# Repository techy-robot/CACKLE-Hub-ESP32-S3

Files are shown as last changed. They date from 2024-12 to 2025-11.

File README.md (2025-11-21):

---
modified: 2025-11-07T22:07:35-07:00
---

# ESP32-S3 Hub

> [!TIP]
> This board is part of a larger modular control board ecosystem, [CACKLE](https://github.com/techy-robot/CACKLE)

This is a 4-driver hub based on the Espressif ESP32-S3FH4 chip. It has two cores powerful running at 240 mhz, and 4mb of flash memory. Other variants of the ESP32-S3 can be used as long as they have built in flash memory.

The ESP32-S3 chip does not *quite* have enough pins for driving 4 motors and several sensors, so some cuts were made. For example, on all 4 ports for the ADCs, only two out of three pins are actually connected. This will work for brushed and brushless FOC control, but it may not work for other use cases. I also had to use the USB lines for a tri-state shift register, which controls all the SPI chip select lines. I am planning on programming the chip via UART, which means that the RS485 lines must be disconnected.

The SPI bus should be able to operate at 80mhz, though this has not been tested yet. For all practical use-cases I am limiting this to 20mhz.

Schematic PDF

Partial 3D picture (headers not shown)
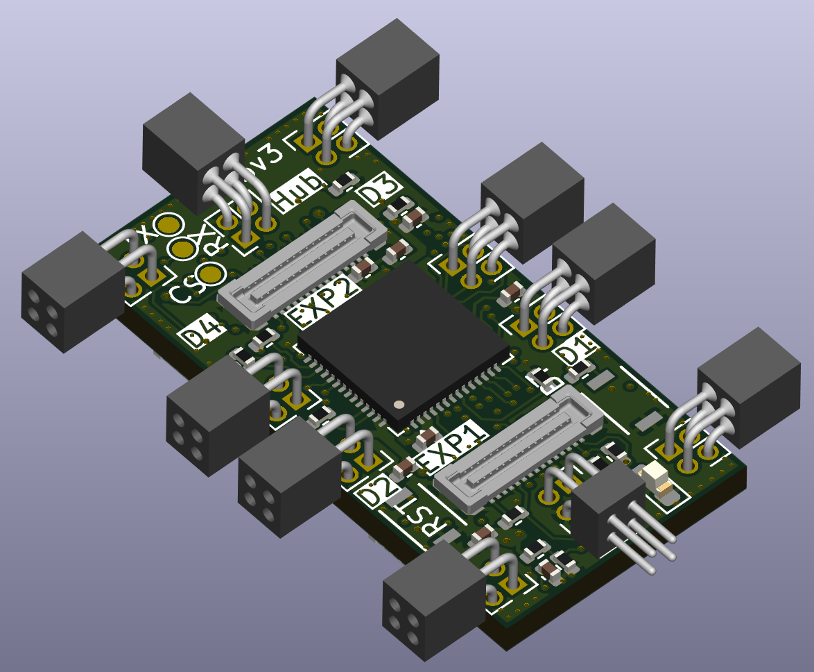
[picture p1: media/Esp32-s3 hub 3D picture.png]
Esp32-s3 hub 3D picture


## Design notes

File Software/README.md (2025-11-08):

# Software

This is based on [Luos Engine](https://www.luos.io/), a lightweight distributed communication engine that aims to make hardware as modular as software. 

Most of the code found here are luos node definitions and driver services for the of the hardware modules, designed to be easily reusable in your project. There are also some tests and example code.

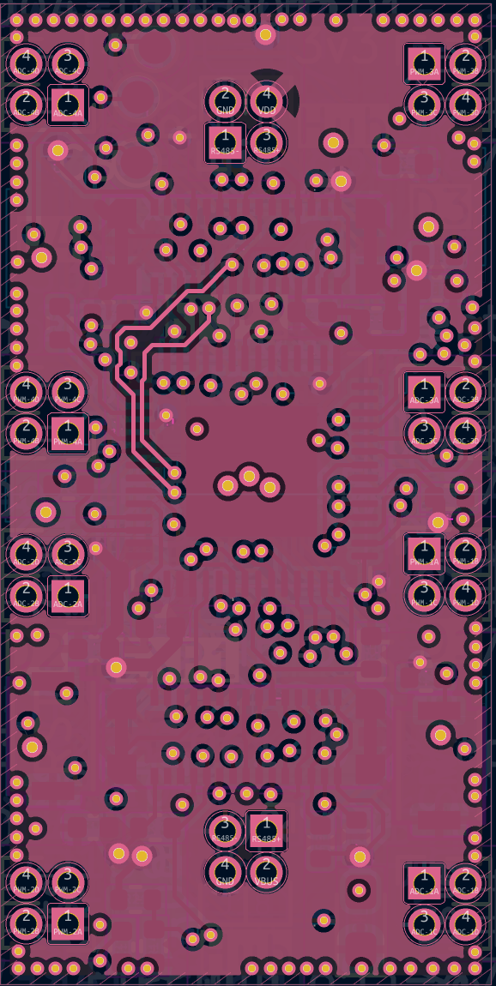
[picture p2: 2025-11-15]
media/ESP32-S3 hub In4.png

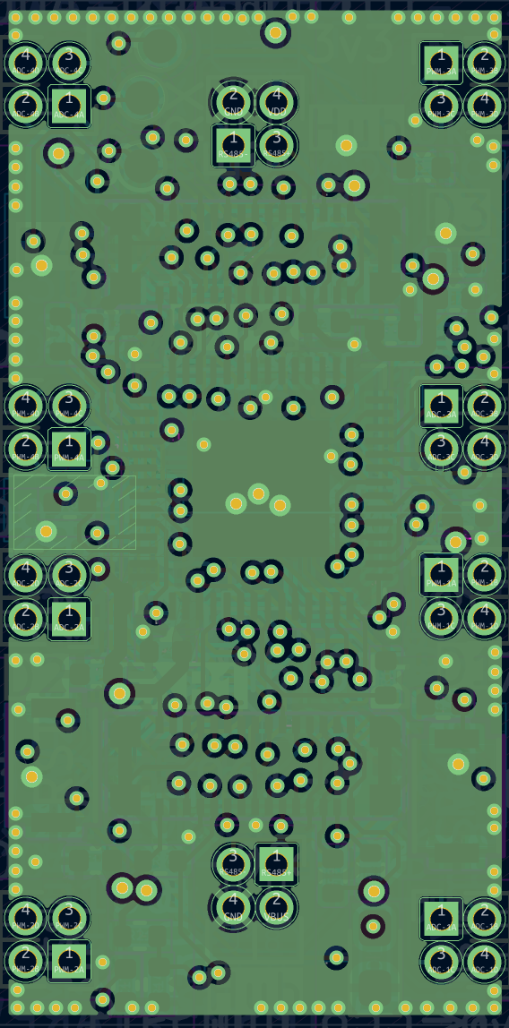
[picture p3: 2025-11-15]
media/ESP32-S3 hub In1.png

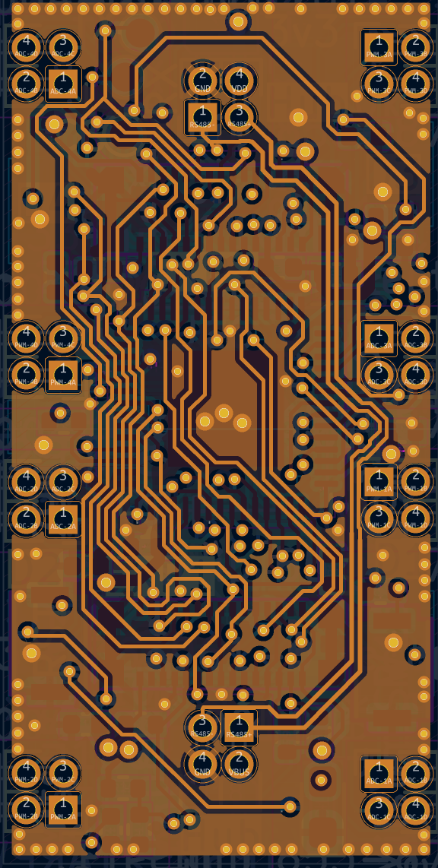
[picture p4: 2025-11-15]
media/ESP32-S3 hub In2.png

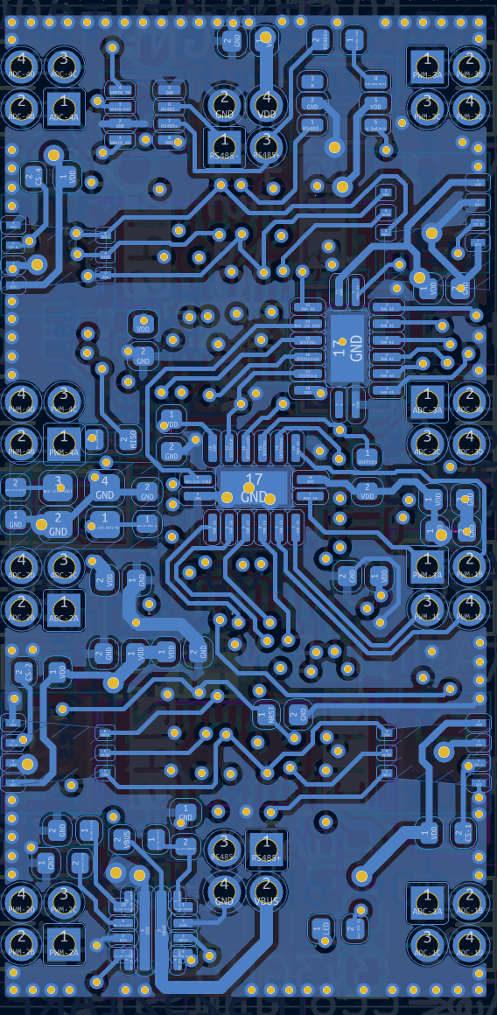
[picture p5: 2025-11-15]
media/ESP32-S3 hub Bottom.png

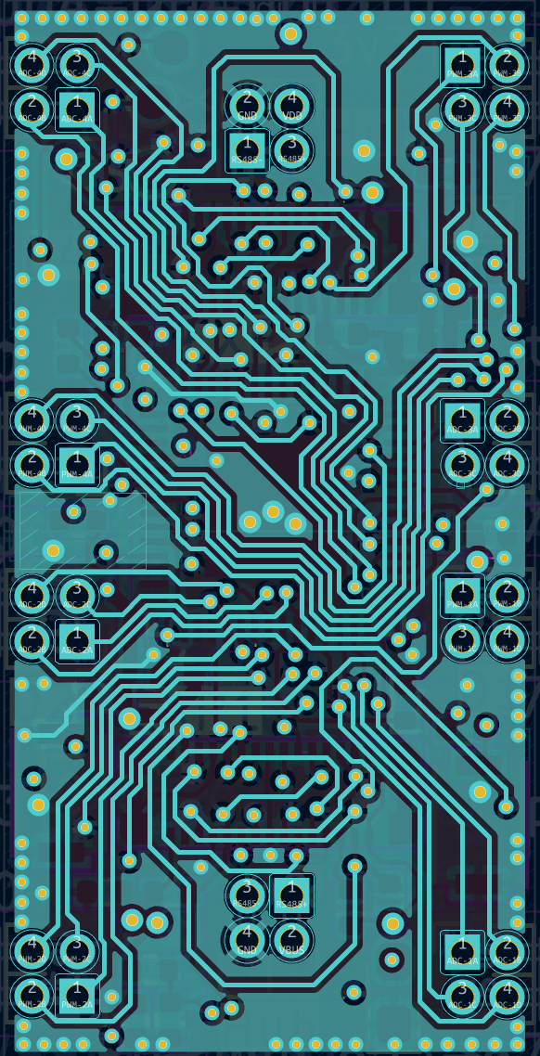
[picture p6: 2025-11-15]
media/ESP32-S3 hub In3.png

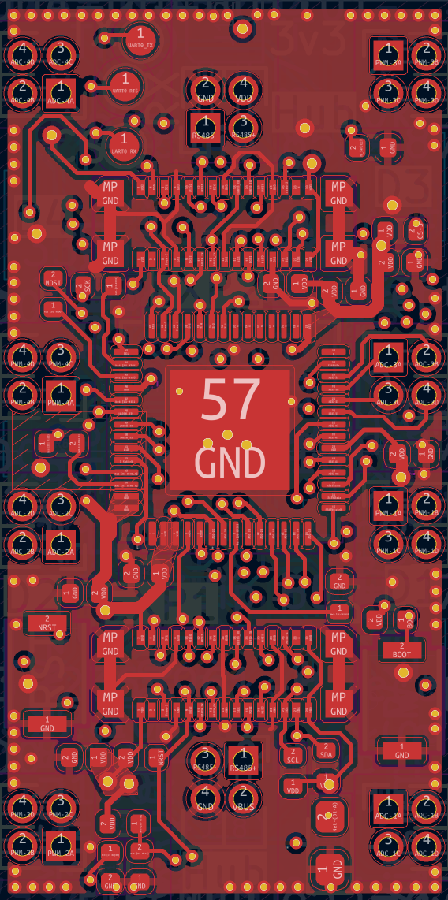
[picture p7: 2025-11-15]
media/ESP32-S3 hub Top.png

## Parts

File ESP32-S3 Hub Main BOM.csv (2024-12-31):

Id | Designator | Footprint | Quantity | Designation | Supplier and ref
1 | D1 | LED_0603_1608Metric_Pad1.05x0.95mm_HandSolder | 1 | 2.6~3.1 Fv Green 5ma
2 | J22 | PinHeader_1x04_P1.27mm_Horizontal | 1 | 1.27mm 4 pin header
3 | C13,C9,C2,C7 | C_0402_1005Metric | 4 | 1uF
4 | C10,C4,C6,C8,C5,C3 | C_0402_1005Metric | 6 | 0.1uF
5 | R8,R9,R7,R20,R19,R11,R18,R2 | R_0402_1005Metric | 8 | 10k
6 | J10,J6,J2,J1,J7,J12,J4,J9 | PinHeader_1x03_P1.27mm_Vertical | 8 | 1.27mm 3pin socket
7 | C12,C11 | C_0402_1005Metric | 2 | 12pF
8 | SW2,SW1 | R-667995_MIT | 2 | Mitsumi R-667996
9 | Y1 | Crystal_SMD_2016-4Pin_2.0x1.6mm | 1 | ABM11-40.000MHZ-B1U-T3, 10ppm, 10pF
10 | FB1 | L_0402_1005Metric | 1 | 120ohm imp @100mhz, 1 amp
11 | U1 | QFN-56-1EP_7x7mm_P0.4mm_EP4x4mm | 1 | ESP32-S3
12 | J16,J13 | TE_mezzanine_rec_3-2363961-0 | 2 | TE 3-2363961-0 receptacle
13 | J21 | PinSocket_1x04_P1.27mm_Vertical | 1 | 1.27mm 4 pin socket
14 | R6 | R_0402_1005Metric | 1 | 22 ohm
15 | R1 | R_0402_1005Metric | 1 | 100k
16 | R10 | R_0402_1005Metric | 1 | 80.6 ohm
17 | C1,C14 | C_0402_1005Metric | 2 | 22uF
18 | U2 | DHVQFN-16-1EP_2.5x3.5mm_P0.5mm_EP1x2mm | 1 | 74HC595
19 | R3,R4,R5 | R_0402_1005Metric | 3 | 33ohm
20 | J14,J17 | TE_mezzanine_conn_3-2363962-0 | 2 | TE 3-2363962-0 Connector
21 | J11,J8,J5,J3 | fpc_7pin_0.3mm_connector Panasonic | 4 | 7 pin FPC 0.3mm Panasonic Y3b
22 | U3 | SOT-583-8 | 1 | THVD1420DRLR

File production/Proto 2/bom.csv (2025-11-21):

Designator | Footprint | Quantity | Value | LCSC Part #
C1, C14 | 402 | 2 | 22uF | C415703
C10, C4, C5, C6, C8 | 402 | 5 | 100nF | C1525
C11, C12 | 201 | 2 | 12pF | C384960
C13, C15, C16, C2, C7, C9 | 402 | 6 | 1uF | C52923
C17 | 402 | 1 | 3.3nF | C272874
C18 | 402 | 1 | 2.7nF | C541392
C19, C20, C21, C22 | 402 | 4 | 10nF | C318576
C3 | 402 | 1 | 10uF | C15525
D1 | 603 | 1 | 2.6~3.1 Fv Green 5ma | C3028858
J1, J10, J12, J15, J2, J4, J6, J7, J9 | Precidip 853-87-004-20-001101 | 9 | Precidip 853-87-004-20-001101
J11, J3, J5, J8 | fpc_7pin_0.3mm_connector Aces | 4 | FPC 0.3mm Aces 51688-0070M
J13, J16 | TE_mezzanine_rec_3-2363961-0 | 2 | TE 3-2363961-0 receptacle | C425103
J18 | Precidip 852-10-004-20-001101 | 1 | Precidip 852-10-004-20-001101
R1, R14 | 402 | 2 | 100k | C25741
R10 | 402 | 1 | 100 ohm | C185392
R11 | 402 | 1 | 470k | C25790
R12 | 402 | 1 | 332k | C138005
R13, R17, R18, R19, R2, R20, R22, R7 | 402 | 8 | 10k | C25744
R15 | 402 | 1 | 6.04k | C321224
R16 | 402 | 1 | 120ohm | C25079
R21 | 402 | 1 | 150k | C25755
R3, R4, R5 | 402 | 3 | 33ohm | C25105
R6 | 201 | 1 | 22 ohm | C155743
R8, R9 | 402 | 2 | 2.2k | C25879
SW1, SW2 | R-667995_MIT | 2 | Mitsumi R-667996 | C4365007
U1 | QFN-56-1EP_7x7mm_P0.4mm_EP4x4mm | 1 | ESP32-S3 FN8 | C3013940
U2, U5 | DHVQFN-16-1EP_2.5x3.5mm_P0.5mm_EP1x2mm | 2 | SN74LV595A | C7083313
U3 | SOT-583-8 | 1 | THVD1420DRLR | C3235555
U4 | QFN-10_10VQFN_2x2mm_P0.5mm | 1 | TPS2521ARPWR | C3662707
U6 | SOT-363_SC-70-6 | 1 | TS5A3159DCK | C46388
Y1 | Crystal_SMD_1612-4Pin_1.6x1.2mm | 1 | 2 pin 40MHZ, 10ppm tol., 20ppm stab., 10pF | C49158191

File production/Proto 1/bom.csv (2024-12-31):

Designator | Footprint | Quantity | Value | LCSC Part #
C1, C14 | 0402 | 2 | 22uF | C415703
C10, C3, C4, C5, C6, C8 | 0402 | 6 | 0.1uF | C1525
C11, C12 | 0402 | 2 | 12pF | C1547
C13, C2, C7, C9 | 0402 | 4 | 1uF | C52923
D1 | 0603 | 1 | 2.6~3.1 Fv Green 5ma | C3028858
FB1 | 0402 | 1 | 120ohm imp @100mhz, 1 amp | C82861
J13, J16 | TE_mezzanine_rec_3-2363961-0 | 2 | TE 3-2363961-0 receptacle | C425103
J14, J17 | TE_mezzanine_conn_3-2363962-0 | 2 | TE 3-2363962-0 Connector | C425104
R1 | 0402 | 1 | 100k | C25741
R10 | 0402 | 1 | 80.6 ohm | C185392
R11, R18, R19, R2, R20, R7, R8, R9 | 0402 | 8 | 10k | C25744
R3, R4, R5 | 0402 | 3 | 33ohm | C25105
R6 | 0402 | 1 | 22 ohm | C25092
SW1, SW2 | R-667995_MIT | 2 | Mitsumi R-667996 | C4365007
U1 | QFN-56-1EP_7x7mm_P0.4mm_EP4x4mm | 1 | ESP32-S3 | C3013940
U2 | DHVQFN-16-1EP_2.5x3.5mm_P0.5mm_EP1x2mm | 1 | 74HC595 | C730243
Y1 | Crystal_SMD_2016-4Pin_2.0x1.6mm | 1 | ABM11-40.000MHZ-B1U-T3, 10ppm, 10pF | C648973

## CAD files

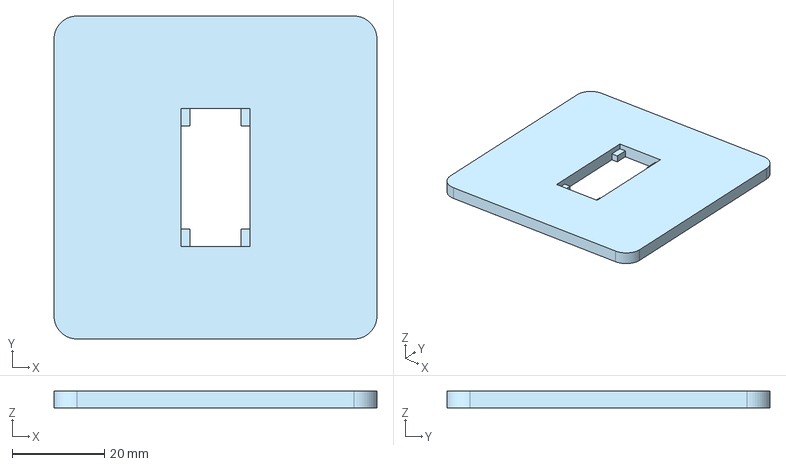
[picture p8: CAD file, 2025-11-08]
ESP32-S3 2nd side Stencil Jig.step
70.0 x 70.0 x 3.60 mm

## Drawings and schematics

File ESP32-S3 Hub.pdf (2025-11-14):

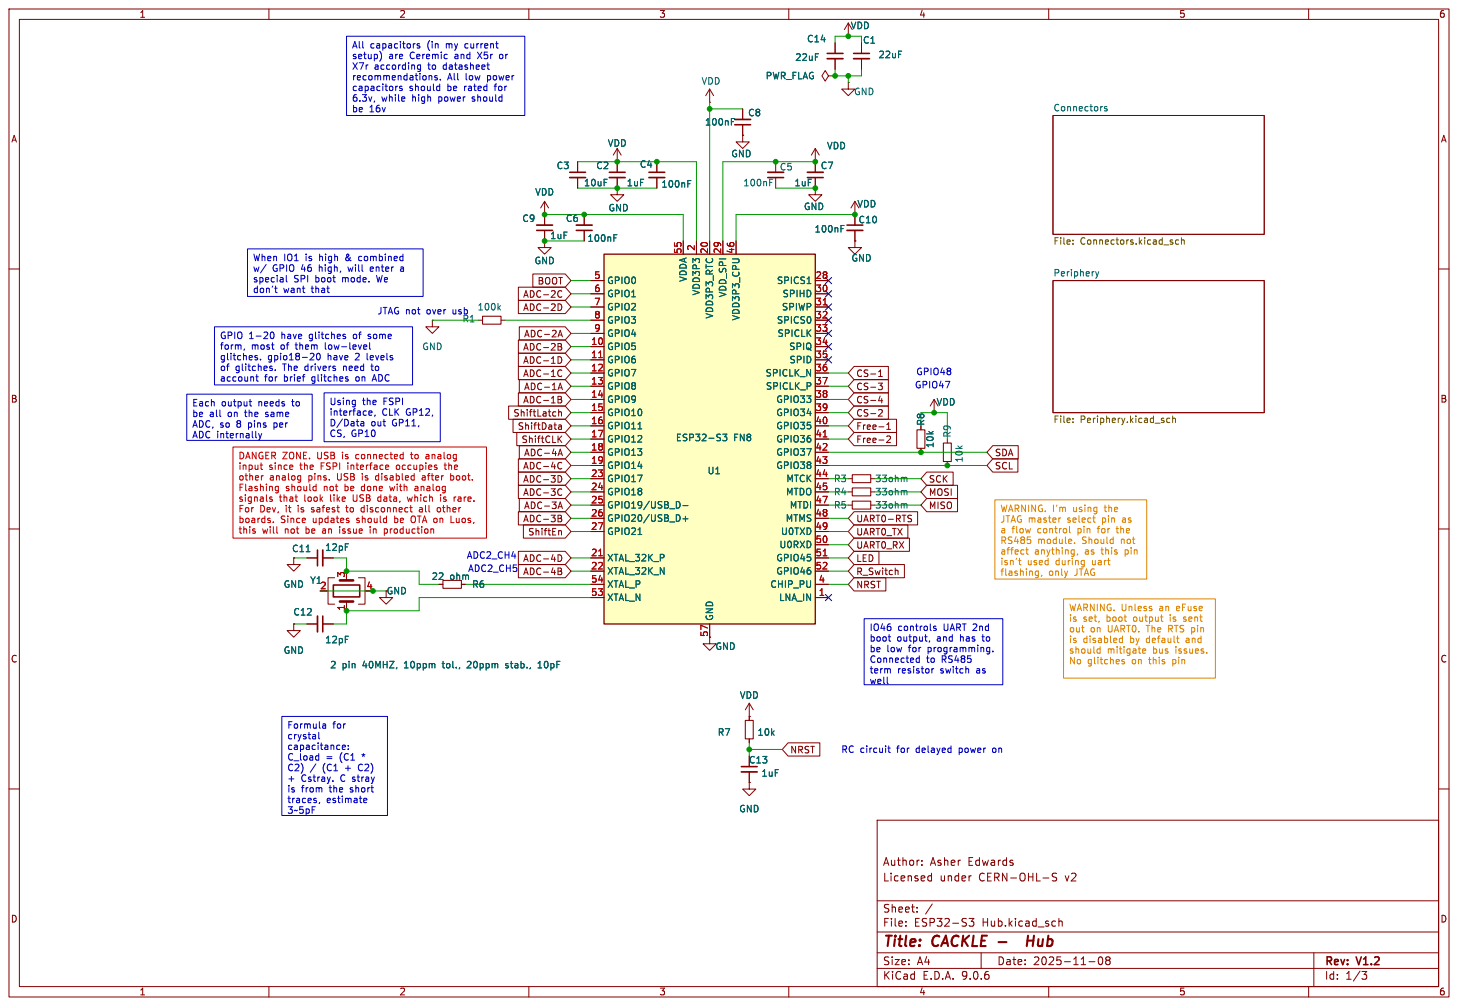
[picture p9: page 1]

Periphery File: Periphery.kicad_sch Connectors File: Connectors.kicad_sch C6

special SPI boot mode. We

this will not be an issue in production

isn't used during uart

boot output, and has to
be low for programming. Connected to RS485

is set, boot output is sent out on UART0. The RTS pin

is from the short
traces, estimate

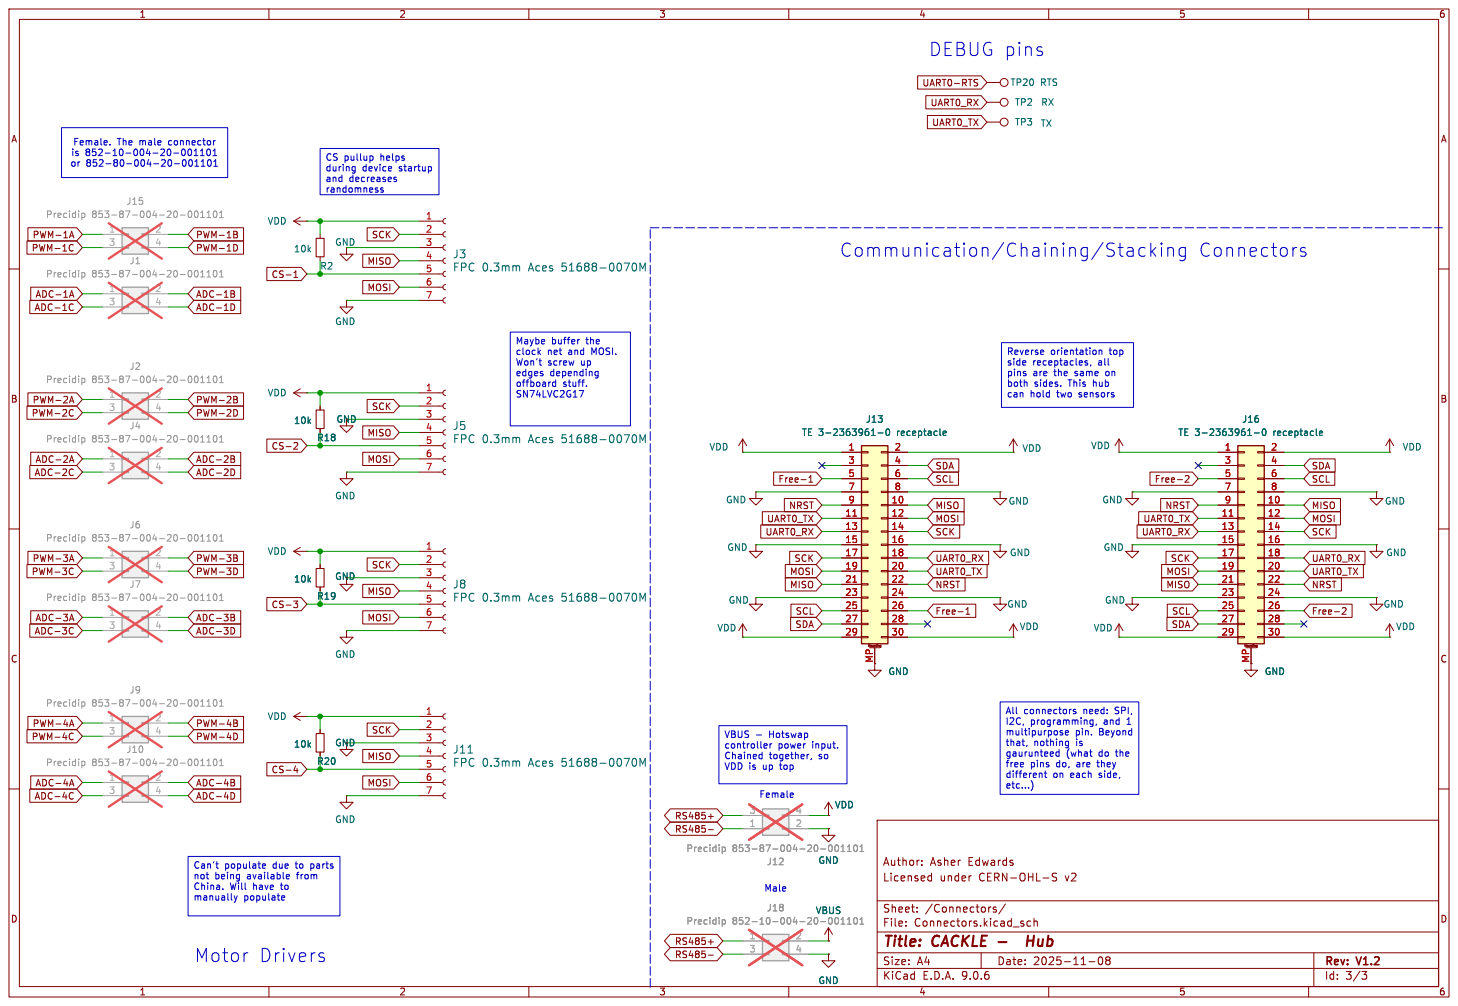
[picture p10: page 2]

clock net and MOSI. Won't screw up

both sides. This hub

can hold two sensors Motor Drivers
PWM-2D

SCK MOSI CS-2 PWM-3B
ADC-2B
CS-3 ADC-2D

SDA MOSI VBUS - Hotswap

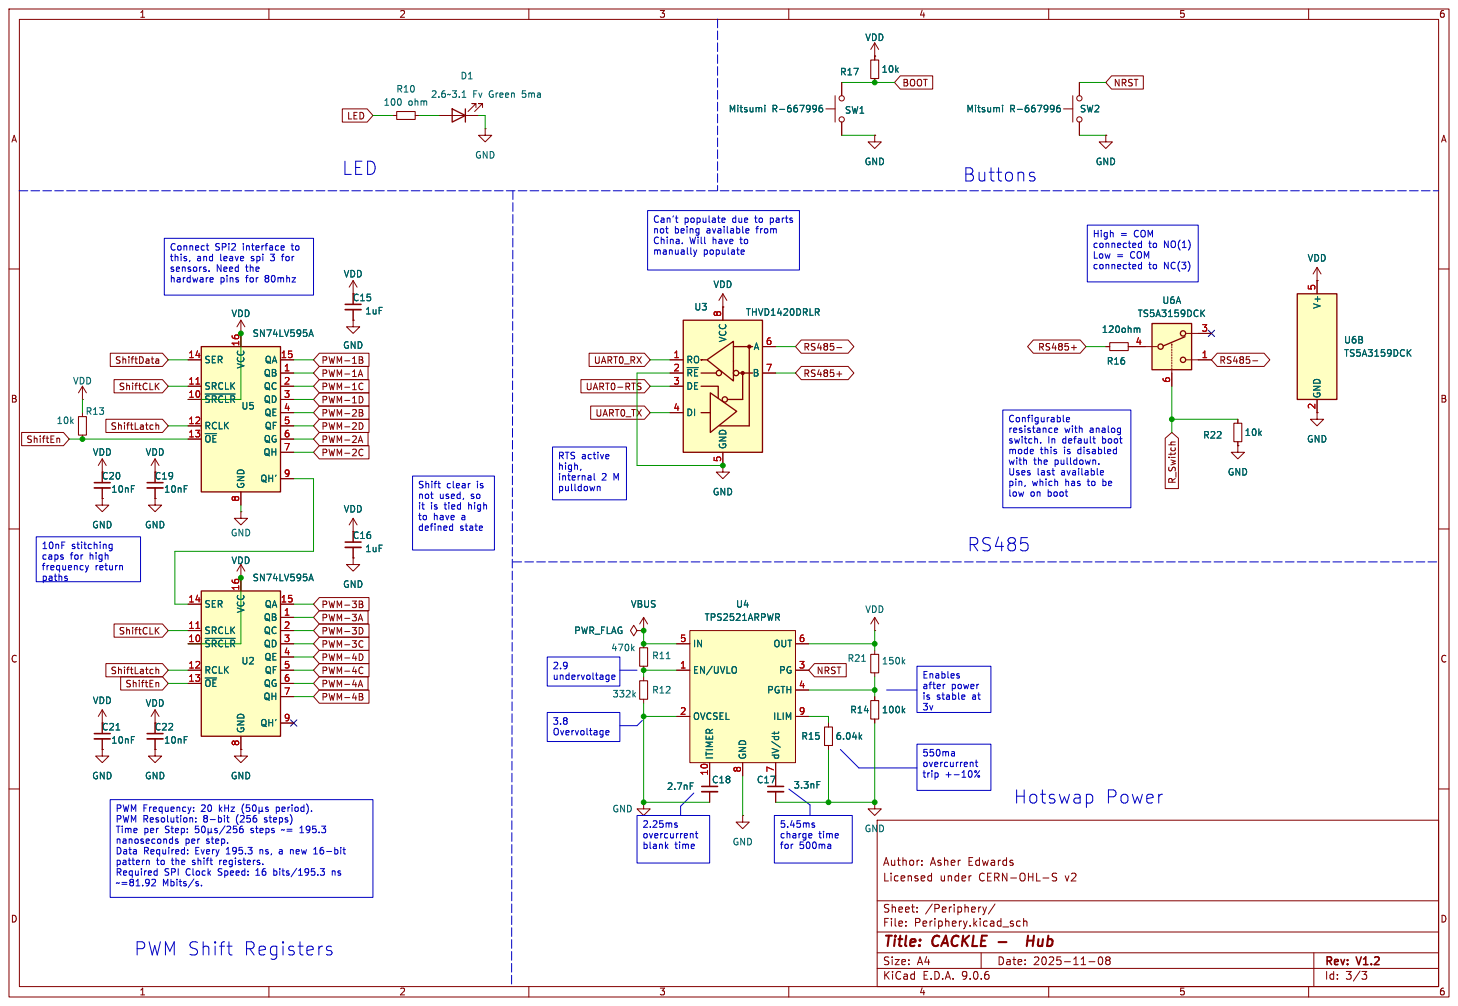
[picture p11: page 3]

this, and leave spi 3 for sensors. Need the

8 QA 15 QB 1 QC 2 QD 3 QE 4 QF 5 QG 6 QH 7 QH' 9 U5SN74LV595A GND

8 QA 15 QB 1 QC 2 QD 3 QE 4 QF 5 QG 6 QH 7 QH' 9 GND

3.8 Overvoltage Shift clear is not used, so

pin, which has to be

it is tied high
to have a

is stable at 3v 10nF stitching
caps for high

8 QA 15 QB 1 QC 2 QD 3 QE 4 QF 5 QG 6 QH 7 QH' 9 VDD VDD

8 dV/dt 7 OUT 6 PG 3 PGTH 4

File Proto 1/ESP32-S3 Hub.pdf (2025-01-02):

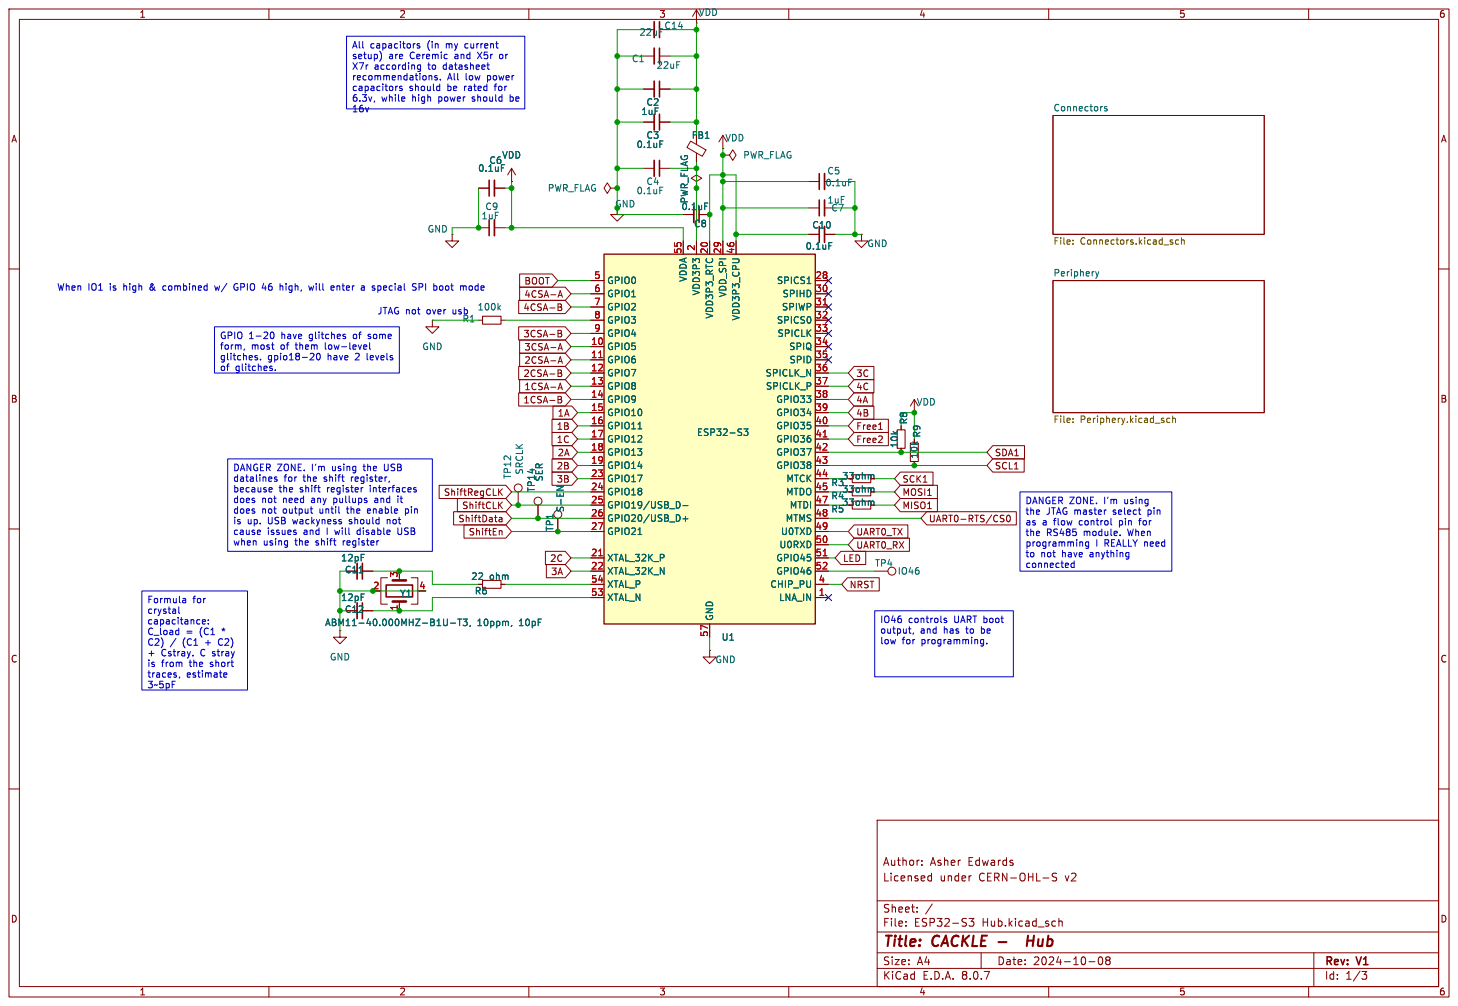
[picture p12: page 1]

Connectors File: Connectors.kicad_sch Periphery File: Periphery.kicad_sch C10

2 VDD3P3_RTC 20 XTAL_32K_P 21 XTAL_32K_N 22 GPIO17 23 GPIO18 24 GPIO19/USB_D- 25 GPIO20/USB_D+ 26 GPIO21 27 SPICS1 28 VDD_SPI 29 SPIHD 30 SPIWP 31 SPICS0 32 SPICLK 33 SPIQ 34 SPID 35 SPICLK_P 37 GPIO33 38 GPIO34 39 CHIP_PU 4 GPIO35 40 GPIO36 41 GPIO37 42 GPIO38 43 MTCK 44 VDD3P3_CPU 46 MTDI 47 MTMS 48 U0TXD 49 GPIO0 5 U0RXD 50 GPIO46 52 XTAL_N 53 XTAL_P 54 VDDA 55 GND 57 GPIO1 6 GPIO2 7 GPIO3 8 GPIO4 9 C10

2 VDD3P3_RTC 20 XTAL_32K_P 21 XTAL_32K_N 22 GPIO17 23 GPIO18 24 GPIO19/USB_D- 25 GPIO20/USB_D+ 26 GPIO21 27 SPICS1 28 VDD_SPI 29 SPIHD 30 SPIWP 31 SPICS0 32 SPICLK 33 SPIQ 34 SPID 35 SPICLK_P 37 GPIO33 38 GPIO34 39 CHIP_PU 4 GPIO35 40 GPIO36 41 GPIO37 42 GPIO38 43 MTCK 44 VDD3P3_CPU 46 MTDI 47 MTMS 48 U0TXD 49 GPIO0 5 U0RXD 50 GPIO46 52 XTAL_N 53 XTAL_P 54 VDDA 55 GND 57 GPIO1 6 GPIO2 7 GPIO3 8 GPIO4 9 U1 ESP32-S3 GND

connected DANGER ZONE. I'm using the USB

the JTAG master select pin
the RS485 module. When
to not have anything

is from the short
traces, estimate

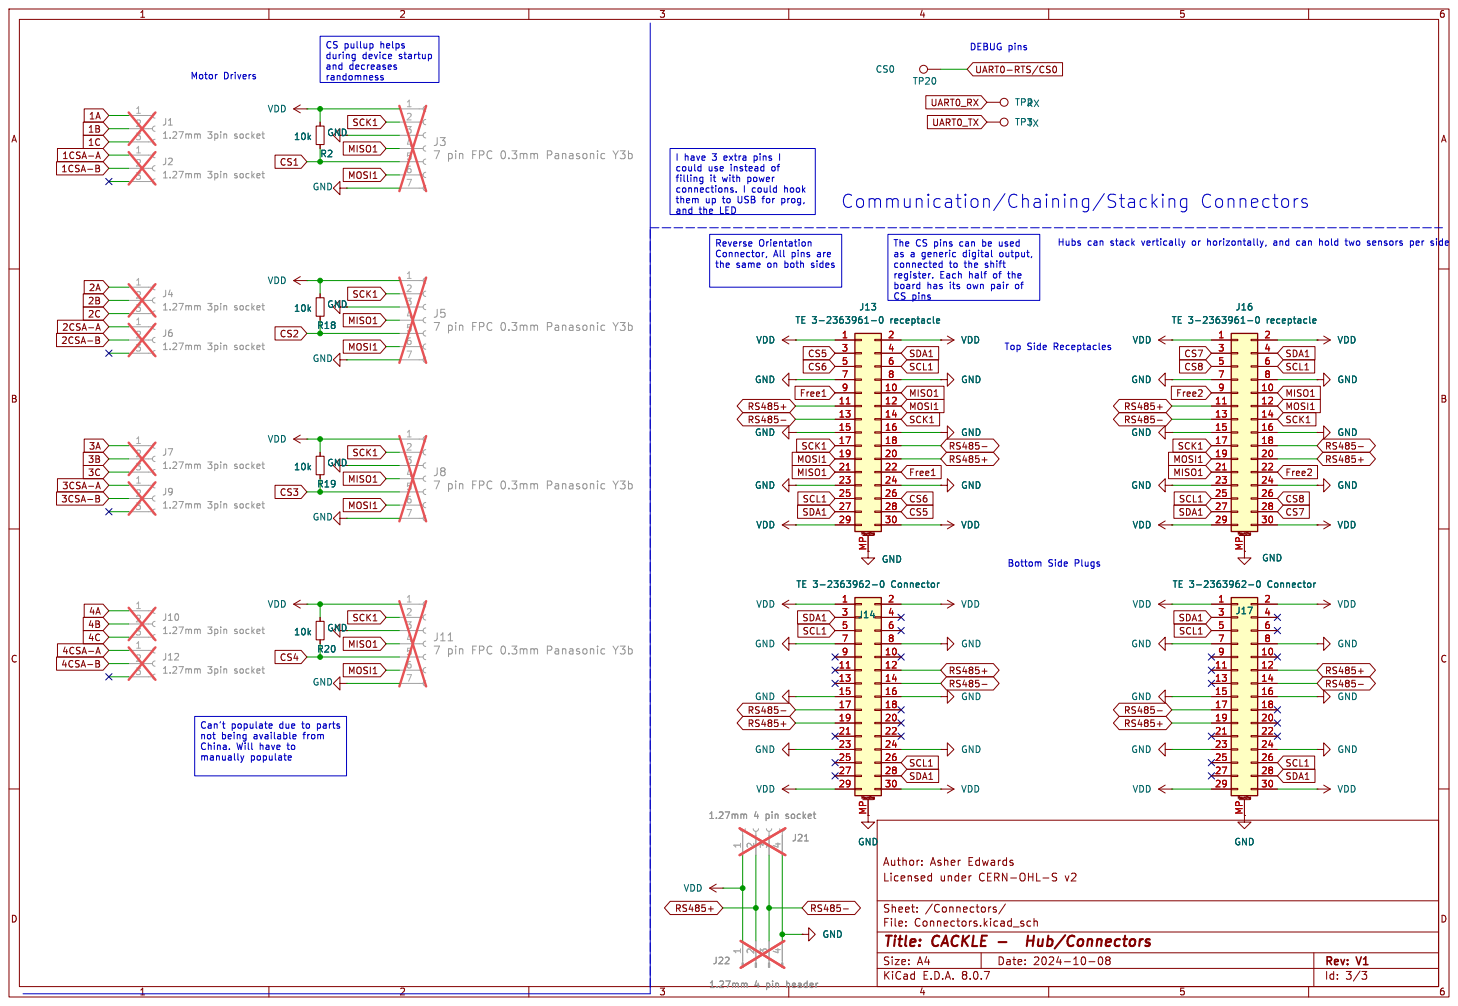
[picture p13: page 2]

board has its own pair of CS pins CS pullup helps
during device startup
and decreases
randomness

Top Side Receptacles DEBUG pins Bottom Side Plugs

I have 3 extra pins I could use instead of

VDD GND GND GND

them up to USB for prog, and the LED

The CS pins can be used

the same on both sides

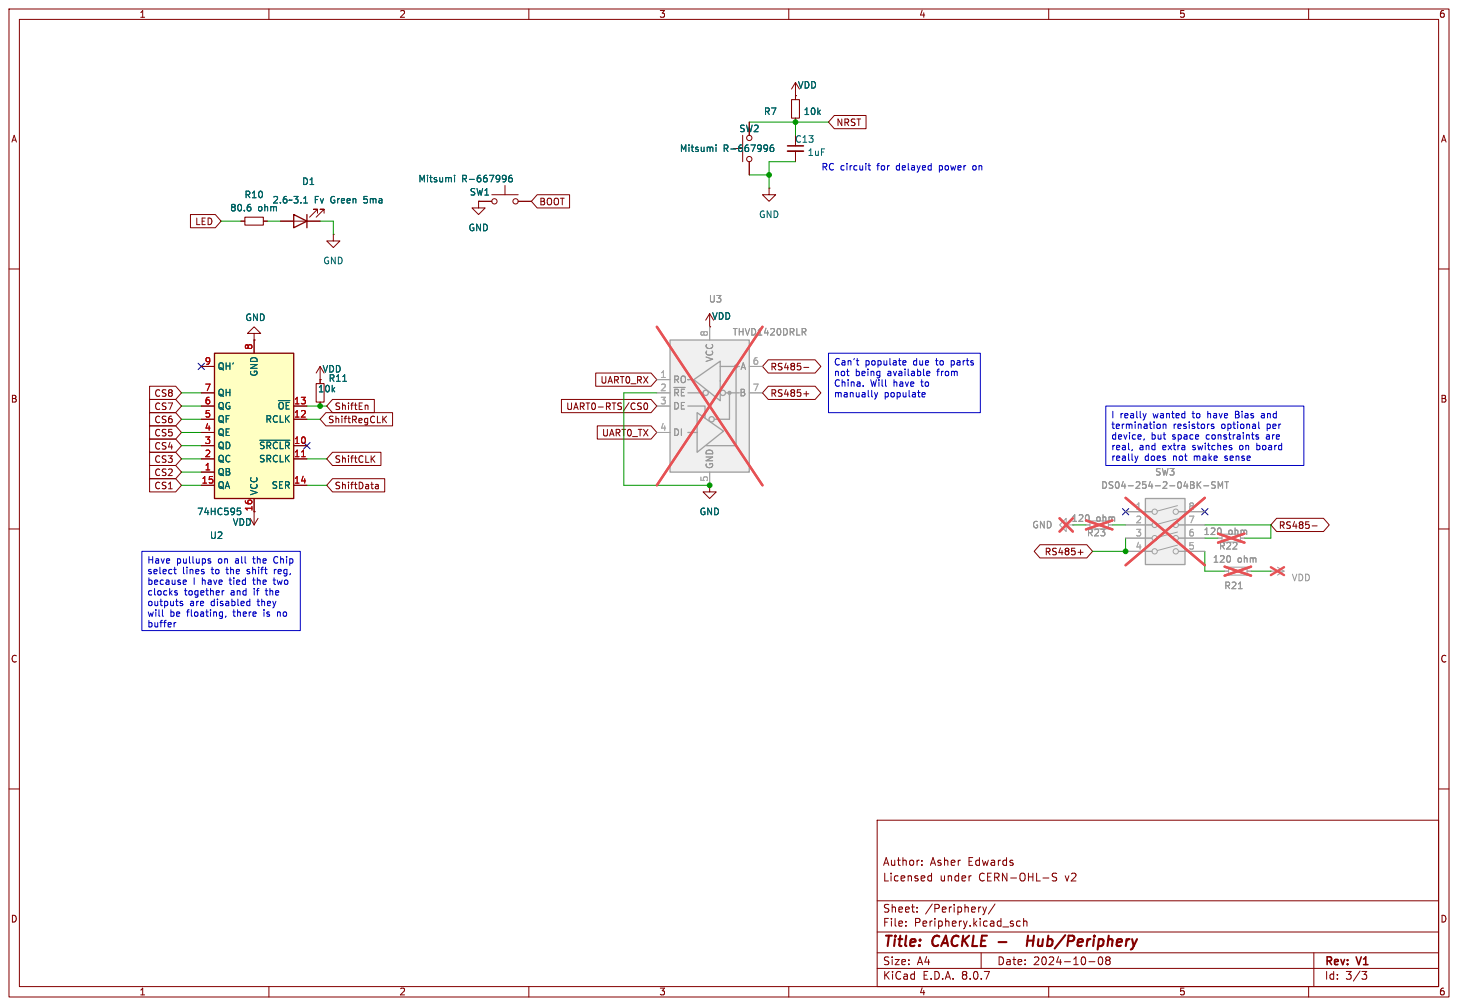
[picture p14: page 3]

really does not make sense VDD GND

I really wanted to have Bias and

real, and extra switches on board

select lines to the shift reg, because I have tied the two

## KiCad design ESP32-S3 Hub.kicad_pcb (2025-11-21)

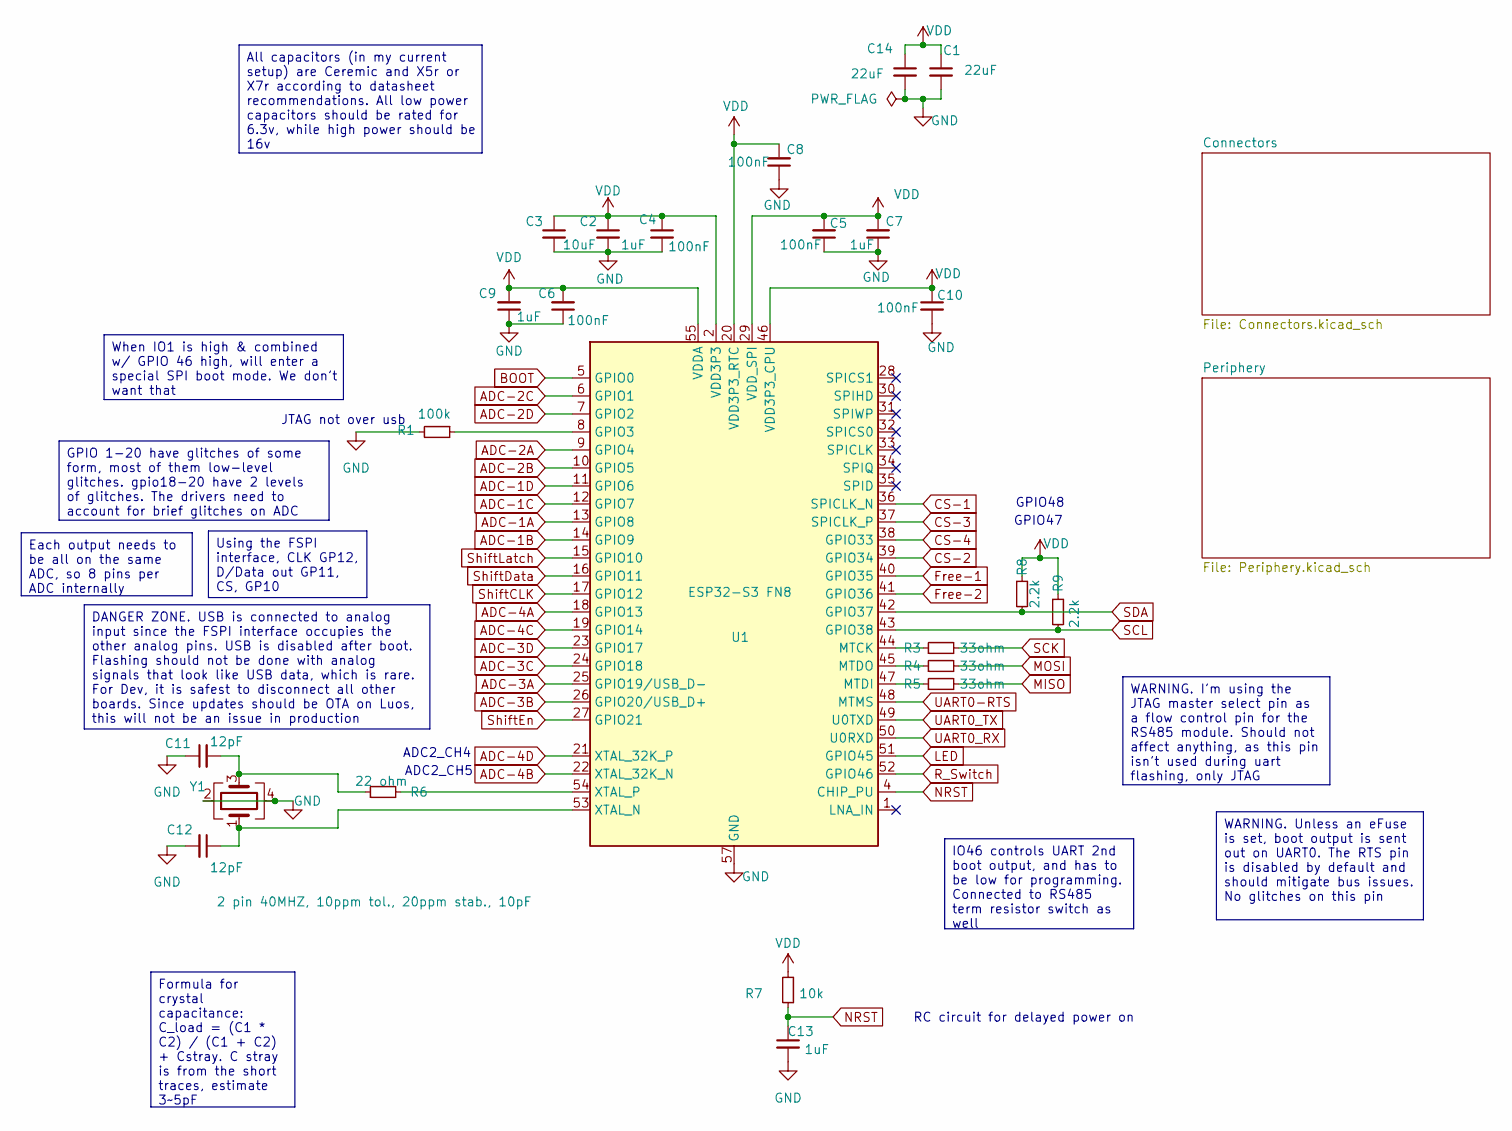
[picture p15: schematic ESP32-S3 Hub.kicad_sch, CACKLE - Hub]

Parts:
C1, C14: 22uF; C_0402_1005Metric; LCSC C415703
C2, C7, C9, C13: 1uF; C_0402_1005Metric; LCSC C52923
C3: 10uF; C_0402_1005Metric; LCSC C15525
C4, C5, C6, C8, C10: 100nF; C_0402_1005Metric; LCSC C1525
C11, C12: 12pF; C_0201_0603Metric; LCSC C384960
R1: 100k; R_0402_1005Metric; LCSC C25741
R3, R4, R5: 33ohm; R_0402_1005Metric; LCSC C25105
R6: 22 ohm; R_0201_0603Metric; LCSC C155743
R7: 10k; R_0402_1005Metric; LCSC C25744
R8, R9: 2.2k; R_0402_1005Metric; LCSC C25879
U1: ESP32-S3 FN8; QFN-56-1EP_7x7mm_P0.4mm_EP4x4mm; LCSC C3013940
Y1: 2 pin 40MHZ, 10ppm tol., 20ppm stab., 10pF; Crystal_SMD_1612-4Pin_1.6x1.2mm; LCSC C49158191

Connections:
ADC-1A: U1.13 (GPIO8); also elsewhere on the board
ADC-1B: U1.14 (GPIO9); also elsewhere on the board
ADC-1C: U1.12 (GPIO7); also elsewhere on the board
ADC-1D: U1.11 (GPIO6); also elsewhere on the board
ADC-2A: U1.9 (GPIO4); also elsewhere on the board
ADC-2B: U1.10 (GPIO5); also elsewhere on the board
ADC-2C: U1.6 (GPIO1); also elsewhere on the board
ADC-2D: U1.7 (GPIO2); also elsewhere on the board
ADC-3A: U1.25 (GPIO19/USB_D-); also elsewhere on the board
ADC-3B: U1.26 (GPIO20/USB_D+); also elsewhere on the board
ADC-3C: U1.24 (GPIO18); also elsewhere on the board
ADC-3D: U1.23 (GPIO17); also elsewhere on the board
ADC-4A: U1.18 (GPIO13); also elsewhere on the board
ADC-4B: U1.22 (XTAL_32K_N); also elsewhere on the board
ADC-4C: U1.19 (GPIO14); also elsewhere on the board
ADC-4D: U1.21 (XTAL_32K_P); also elsewhere on the board
BOOT: U1.5 (GPIO0); also elsewhere on the board
CS-1: U1.36 (SPICLK_N); also elsewhere on the board
CS-2: U1.39 (GPIO34); also elsewhere on the board
CS-3: U1.37 (SPICLK_P); also elsewhere on the board
CS-4: U1.38 (GPIO33); also elsewhere on the board
Free-1: U1.40 (GPIO35); also elsewhere on the board
Free-2: U1.41 (GPIO36); also elsewhere on the board
GND: C1.2, C2.2, C3.2, C4.2, C5.1, C6.1, C7.1, C8.1, C9.1, C10.2, C11.1, C12.2, C13.2, C14.2, R1.2, U1.57 (GND), Y1.2, Y1.4; also elsewhere on the board
LED: U1.51 (GPIO45); also elsewhere on the board
MISO: R5.2; also elsewhere on the board
MOSI: R4.2; also elsewhere on the board
NRST: C13.1, R7.1, U1.4 (CHIP_PU); also elsewhere on the board
unnamed: C11.2, R6.1, Y1.3
unnamed: R1.1, U1.8 (GPIO3)
unnamed: R3.1, U1.44 (MTCK)
unnamed: R5.1, U1.47 (MTDI)
unnamed: R4.1, U1.45 (MTDO)
unnamed: C12.1, U1.53 (XTAL_N), Y1.1
unnamed: R6.2, U1.54 (XTAL_P)
R_Switch: U1.52 (GPIO46); also elsewhere on the board
SCK: R3.2; also elsewhere on the board
SCL: R9.2, U1.43 (GPIO38); also elsewhere on the board
SDA: R8.2, U1.42 (GPIO37); also elsewhere on the board
ShiftCLK: U1.17 (GPIO12); also elsewhere on the board
ShiftData: U1.16 (GPIO11); also elsewhere on the board
ShiftEn: U1.27 (GPIO21); also elsewhere on the board
ShiftLatch: U1.15 (GPIO10); also elsewhere on the board
UART0-RTS: U1.48 (MTMS); also elsewhere on the board
UART0_RX: U1.50 (U0RXD); also elsewhere on the board
UART0_TX: U1.49 (U0TXD); also elsewhere on the board
VDD: C1.1, C2.1, C3.1, C4.1, C5.2, C6.2, C7.2, C8.2, C9.2, C10.1, C14.1, R7.2, R8.1, R9.1, U1.2 (VDD3P3), U1.3 (VDD3P3), U1.20 (VDD3P3_RTC), U1.29 (VDD_SPI), U1.46 (VDD3P3_CPU), U1.55 (VDDA), U1.56 (VDDA); also elsewhere on the board

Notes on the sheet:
GPIO48
JTAG not over usb
GPIO47
RC circuit for delayed power on
ADC2_CH4
ADC2_CH5
WARNING. I'm using the JTAG master select pin as a flow control pin for the RS485 module. Should not affect anything, as this pin isn't used during uart flashing, only JTAG
DANGER ZONE. USB is connected to analog input since the FSPI interface occupies the other analog pins. USB is disabled after boot. Flashing should not be done with analog signals that look like USB data, which is rare. For Dev, it is safest to disconnect all other boards. Since updates should be OT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
WARNING. Unless an eFuse is set, boot output is sent out on UART0. The RTS pin is disabled by default and should mitigate bus issues. No glitches on this pin
All capacitors (in my current setup) are Ceremic and X5r or X7r according to datasheet recommendations. All low power capacitors should be rated for 6.3v, while high power should be 16v
IO46 controls UART 2nd boot output, and has to be low for programming. Connected to RS485 term resistor switch as well
Each output needs to be all on the same ADC, so 8 pins per ADC internally
GPIO 1-20 have glitches of some form, most of them low-level glitches. gpio18-20 have 2 levels of glitches. The drivers need to account for brief glitches on ADC
Using the FSPI interface, CLK GP12, D/Data out GP11, CS, GP10
When IO1 is high & combined w/ GPIO 46 high, will enter a special SPI boot mode. We don't want that
Formula for crystal capacitance: C_load = (C1 * C2) / (C1 + C2) + Cstray. C stray is from the short traces, estimate 3~5pF

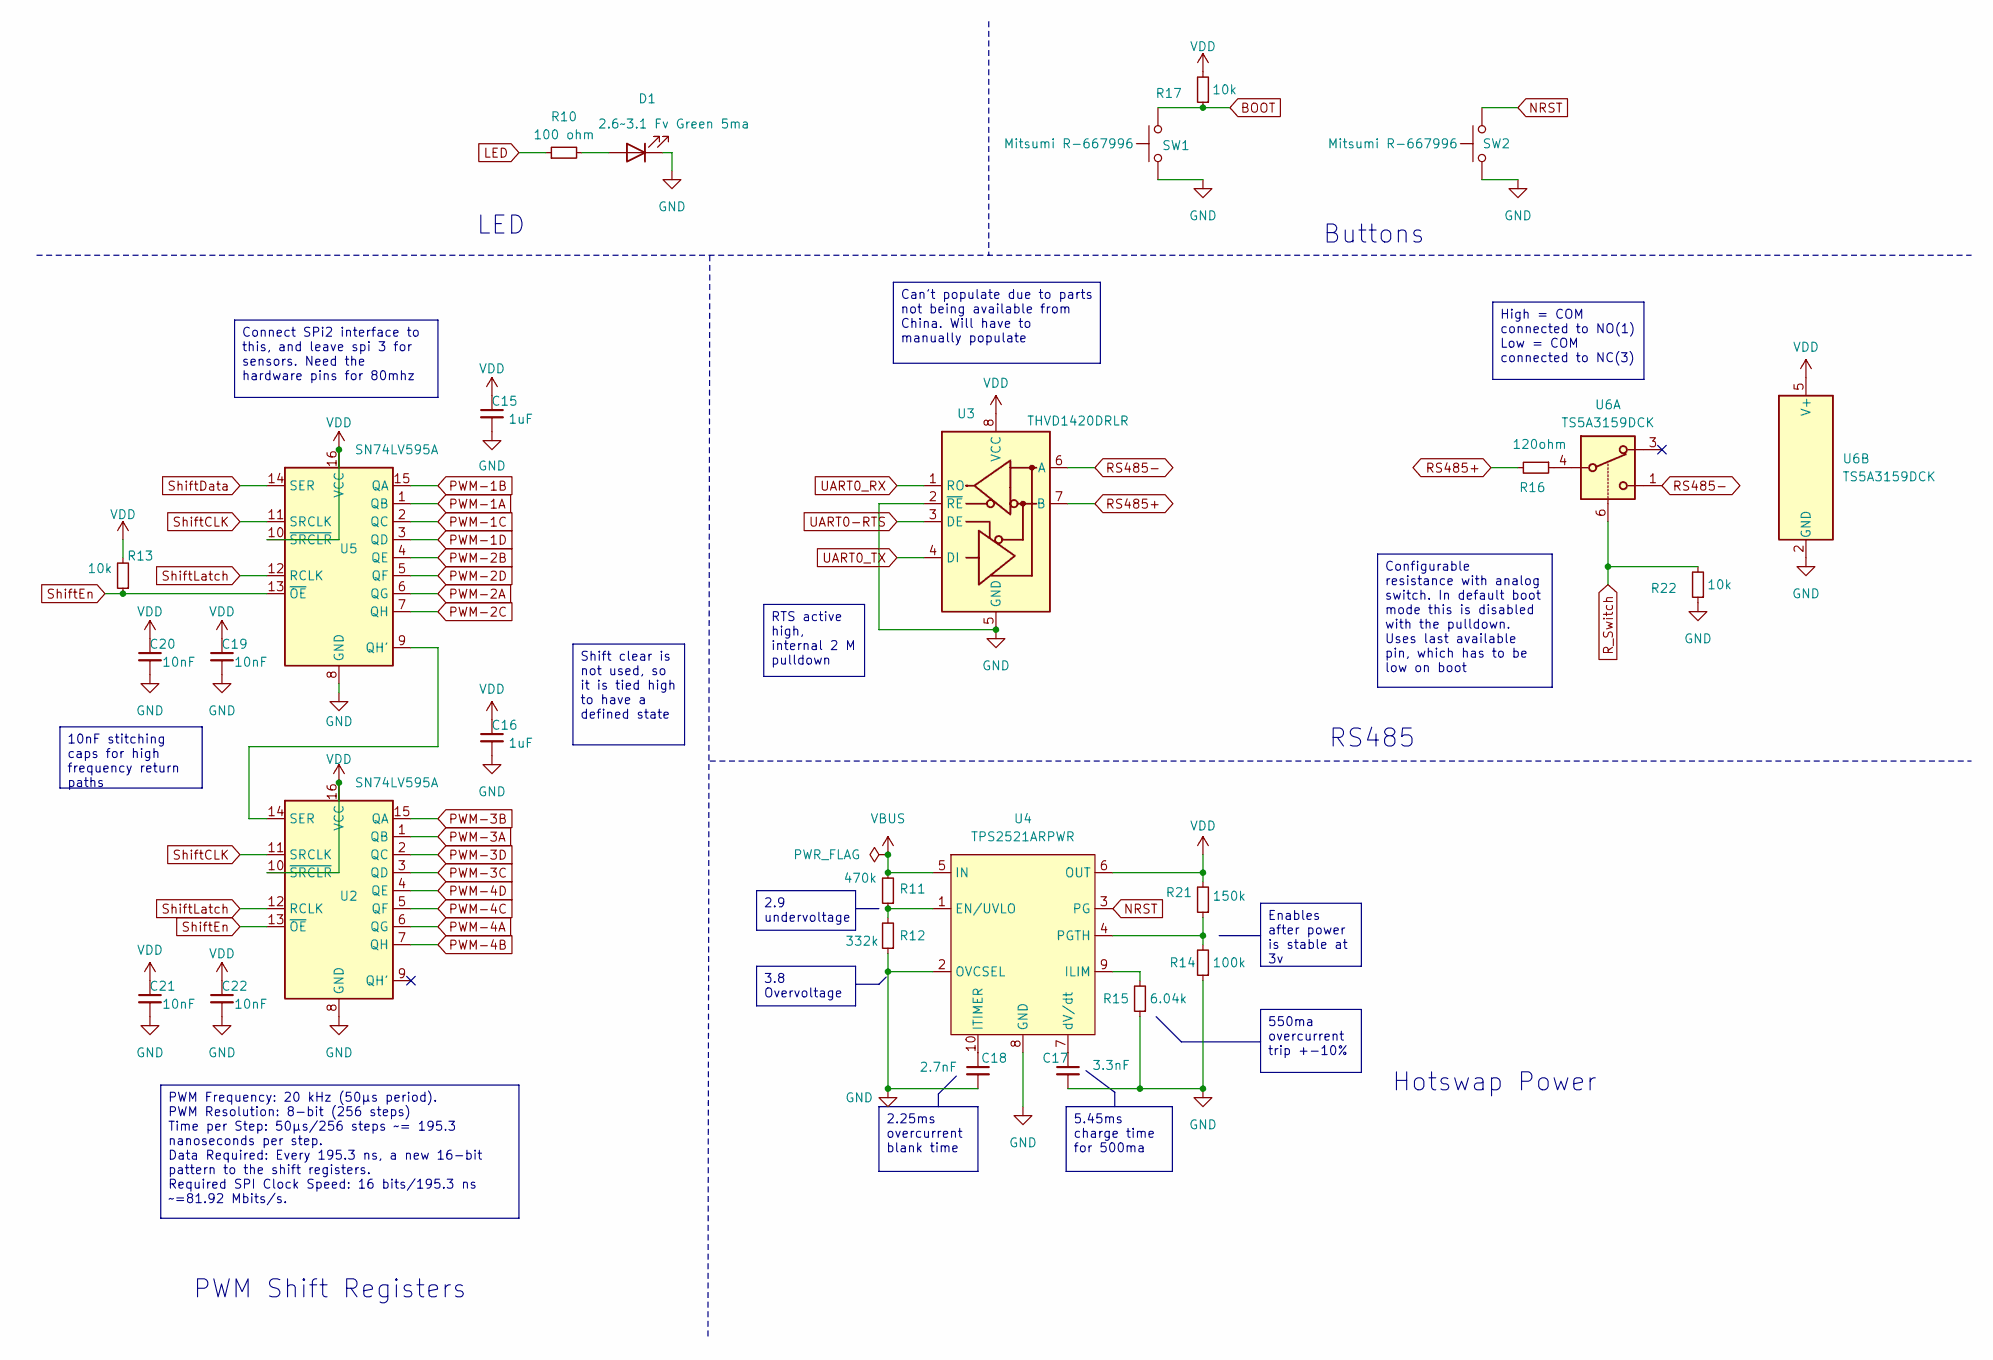
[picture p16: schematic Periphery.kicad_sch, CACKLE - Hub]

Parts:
C15, C16: 1uF; C_0402_1005Metric; LCSC C52923
C17: 3.3nF; C_0402_1005Metric; LCSC C272874
C18: 2.7nF; C_0402_1005Metric; LCSC C541392
C19, C20, C21, C22: 10nF; C_0402_1005Metric; LCSC C318576
D1: 2.6~3.1 Fv Green 5ma; LED_0603_1608Metric_Pad1.05x0.95mm_HandSolder; LCSC C3028858
R10: 100 ohm; R_0402_1005Metric; LCSC C185392
R11: 470k; R_0402_1005Metric; LCSC C25790
R12: 332k; R_0402_1005Metric; LCSC C138005
R13, R17, R22: 10k; R_0402_1005Metric; LCSC C25744
R14: 100k; R_0402_1005Metric; LCSC C25741
R15: 6.04k; R_0402_1005Metric; LCSC C321224
R16: 120ohm; R_0402_1005Metric; LCSC C25079
R21: 150k; R_0402_1005Metric; LCSC C25755
SW1, SW2: Mitsumi R-667996; R-667995_MIT; LCSC C4365007
U2, U5: SN74LV595A; DHVQFN-16-1EP_2.5x3.5mm_P0.5mm_EP1x2mm; LCSC C7083313
U3: THVD1420DRLR; SOT-583-8; LCSC C3235555
U4: TPS2521ARPWR; QFN-10_10VQFN_2x2mm_P0.5mm; LCSC C3662707
U6: TS5A3159DCK; SOT-363_SC-70-6; LCSC C46388

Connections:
BOOT: R17.1, SW1.2; also elsewhere on the board
GND: C15.2, C16.2, C17.2, C18.2, C19.2, C20.2, C21.2, C22.2, D1.1 (K), R12.1, R14.1, R15.1, R22.1, SW1.1, SW2.1, U2.8 (GND), U2.17, U3.2 (~RE), U3.5 (GND), U4.2 (OVCSEL), U4.8 (GND), U5.8 (GND), U5.17, U6.2 (GND); also elsewhere on the board
LED: R10.1; also elsewhere on the board
NRST: SW2.2, U4.3 (PG); also elsewhere on the board
unnamed: D1.2 (A), R10.2
unnamed: R16.1, U6.4
unnamed: U2.14 (SER), U5.9 (QH')
unnamed: R11.1, R12.2, U4.1 (EN/UVLO)
unnamed: R15.2, U4.9 (ILIM)
unnamed: C18.1, U4.10 (ITIMER)
unnamed: R14.2, R21.1, U4.4 (PGTH)
unnamed: C17.1, U4.7 (dV/dt)
PWM-1A: U5.1 (QB); also elsewhere on the board
PWM-1B: U5.15 (QA); also elsewhere on the board
PWM-1C: U5.2 (QC); also elsewhere on the board
PWM-1D: U5.3 (QD); also elsewhere on the board
PWM-2A: U5.6 (QG); also elsewhere on the board
PWM-2B: U5.4 (QE); also elsewhere on the board
PWM-2C: U5.7 (QH); also elsewhere on the board
PWM-2D: U5.5 (QF); also elsewhere on the board
PWM-3A: U2.1 (QB); also elsewhere on the board
PWM-3B: U2.15 (QA); also elsewhere on the board
PWM-3C: U2.3 (QD); also elsewhere on the board
PWM-3D: U2.2 (QC); also elsewhere on the board
PWM-4A: U2.6 (QG); also elsewhere on the board
PWM-4B: U2.7 (QH); also elsewhere on the board
PWM-4C: U2.5 (QF); also elsewhere on the board
PWM-4D: U2.4 (QE); also elsewhere on the board
RS485+: R16.2, U3.7 (B); also elsewhere on the board
RS485-: U3.6 (A), U6.1; also elsewhere on the board
R_Switch: R22.2, U6.6; also elsewhere on the board
ShiftCLK: U2.11 (SRCLK), U5.11 (SRCLK); also elsewhere on the board
ShiftData: U5.14 (SER); also elsewhere on the board
ShiftEn: R13.1, U2.13 (~OE), U5.13 (~OE); also elsewhere on the board
ShiftLatch: U2.12 (RCLK), U5.12 (RCLK); also elsewhere on the board
UART0-RTS: U3.3 (DE); also elsewhere on the board
UART0_RX: U3.1 (RO); also elsewhere on the board
UART0_TX: U3.4 (DI); also elsewhere on the board
VBUS: R11.2, U4.5 (IN); also elsewhere on the board
VDD: C15.1, C16.1, C19.1, C20.1, C21.1, C22.1, R13.2, R17.2, R21.2, U2.10 (~SRCLR), U2.16 (VCC), U3.8 (VCC), U4.6 (OUT), U5.10 (~SRCLR), U5.16 (VCC), U6.5 (V+); also elsewhere on the board

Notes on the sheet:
PWM Shift Registers
LED
Buttons
RS485
Hotswap Power
Enables after power is stable at 3v
High = COM connected to NO(1) Low = COM connected to NC(3)
RTS active high, internal 2 M pulldown
Can't populate due to parts not being available from China. Will have to manually populate
Shift clear is not used, so it is tied high to have a defined state
Configurable resistance with analog switch. In default boot mode this is disabled with the pulldown. Uses last available pin, which has to be low on boot
2.25ms overcurrent blank time
10nF stitching caps for high frequency return paths
5.45ms charge time for 500ma
PWM Frequency: 20 kHz (50μs period). PWM Resolution: 8-bit (256 steps) Time per Step: 50μs/256 steps ~= 195.3 nanoseconds per step. Data Required: Every 195.3 ns, a new 16-bit pattern to the shift registers. Required SPI Clock Speed: 16 bits/195.3 ns ~=81.92 Mbits/s.
Connect SPi2 interface to this, and leave spi 3 for sensors. Need the hardware pins for 80mhz
3.8 Overvoltage
550ma overcurrent trip +-10%
2.9 undervoltage

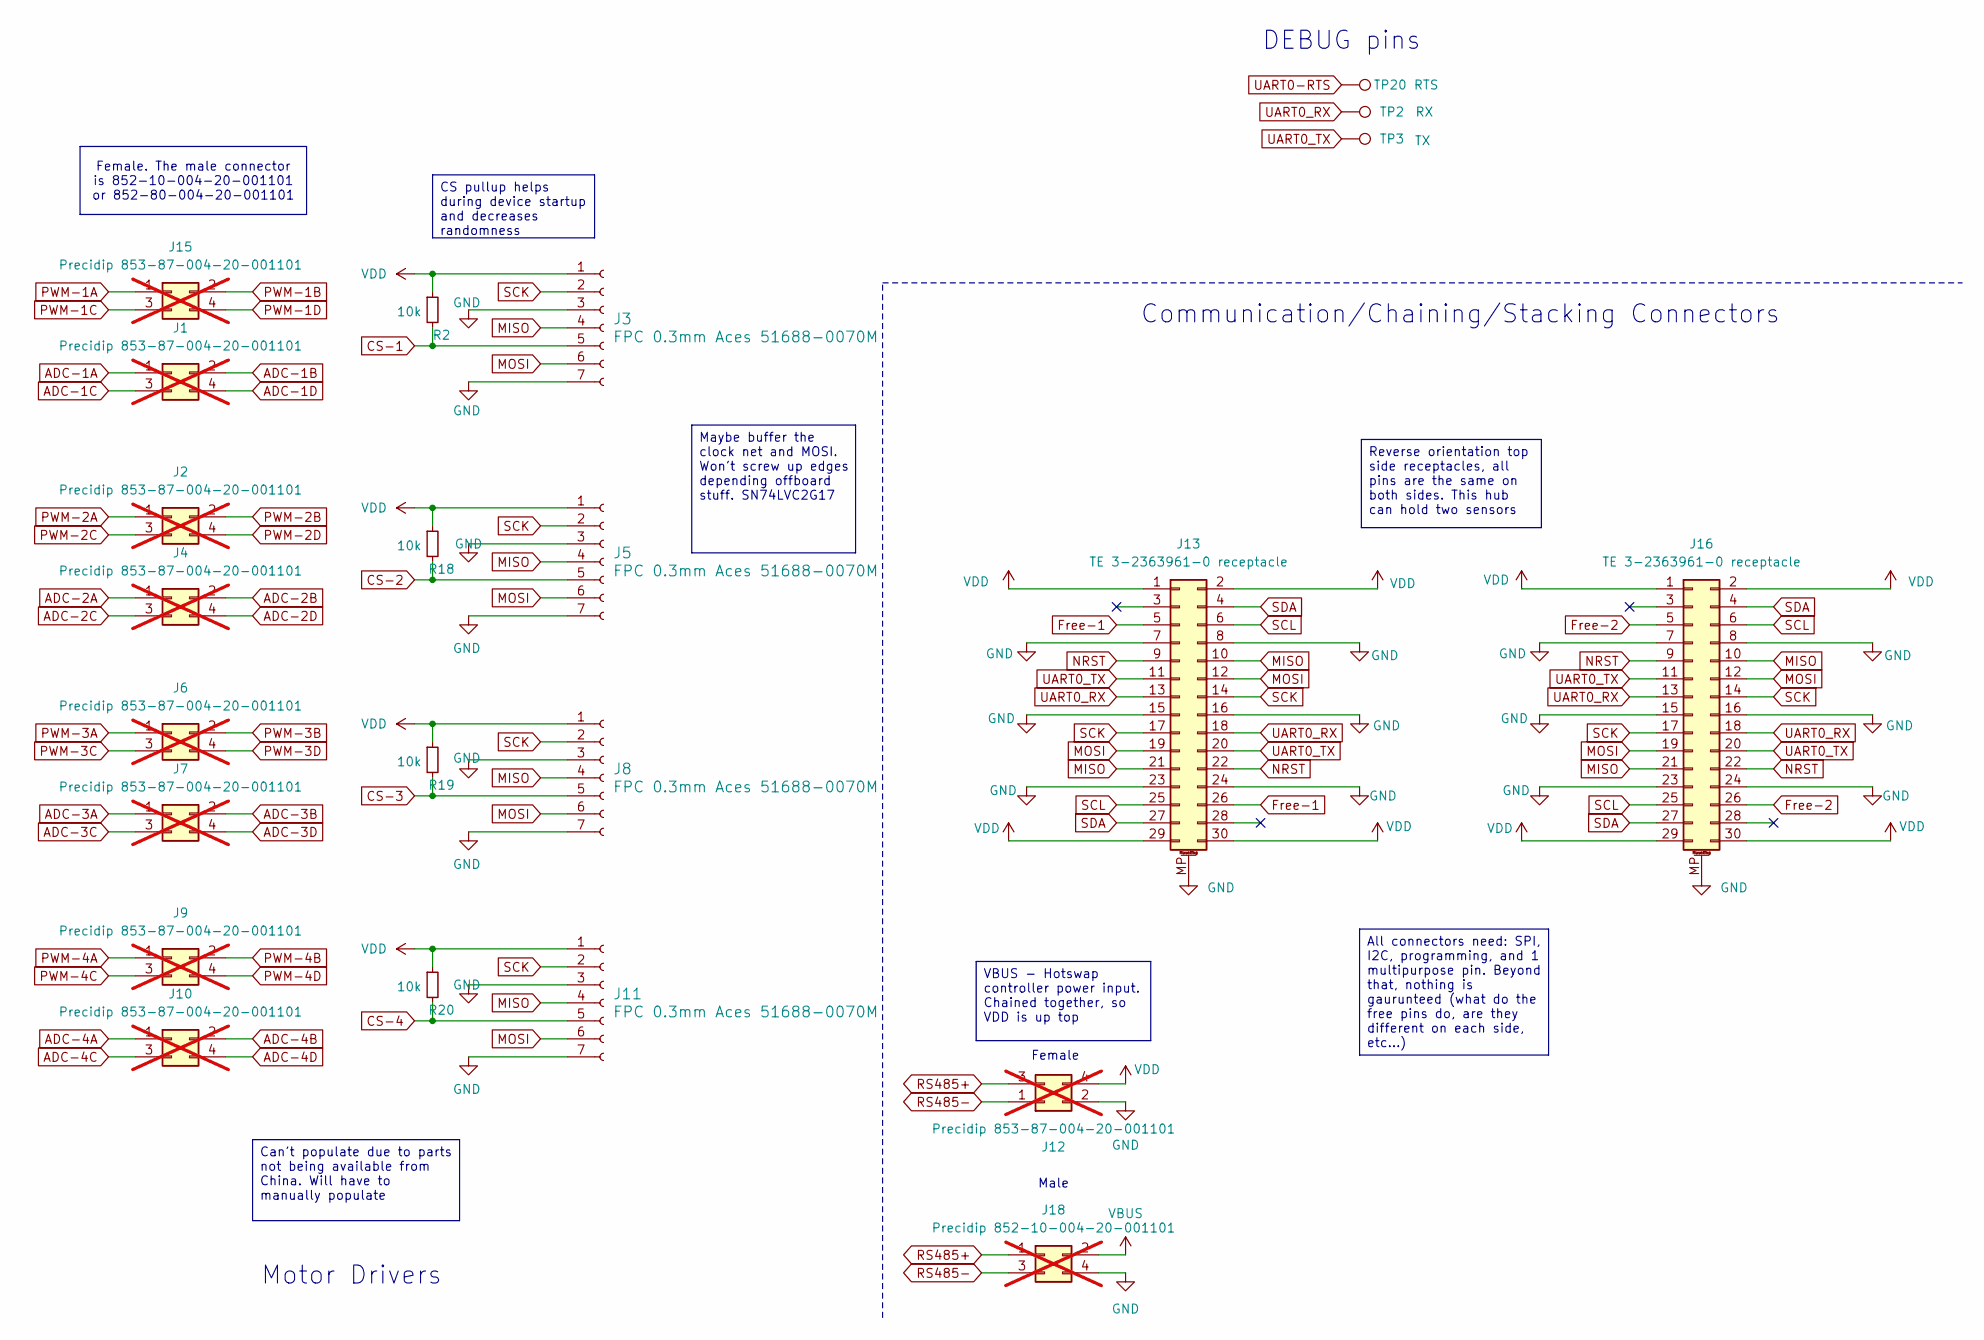
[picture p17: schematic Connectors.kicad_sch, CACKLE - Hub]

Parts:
J1, J2, J4, J6, J7, J9, J10, J12, J15: Precidip 853-87-004-20-001101; not fitted
J3, J5, J8, J11: FPC 0.3mm Aces 51688-0070M; fpc_7pin_0.3mm_connector Aces
J13, J16: TE 3-2363961-0 receptacle; TE_mezzanine_rec_3-2363961-0; LCSC C425103
J18: Precidip 852-10-004-20-001101; not fitted
R2, R18, R19, R20: 10k; R_0402_1005Metric; LCSC C25744
TP2: RX; TestPoint_Pad_D1.0mm
TP3: TX; TestPoint_Pad_D1.0mm
TP20: RTS; TestPoint_Pad_D1.0mm

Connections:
ADC-1A: J1.1; also elsewhere on the board
ADC-1B: J1.2; also elsewhere on the board
ADC-1C: J1.3; also elsewhere on the board
ADC-1D: J1.4; also elsewhere on the board
ADC-2A: J4.1; also elsewhere on the board
ADC-2B: J4.2; also elsewhere on the board
ADC-2C: J4.3; also elsewhere on the board
ADC-2D: J4.4; also elsewhere on the board
ADC-3A: J7.1; also elsewhere on the board
ADC-3B: J7.2; also elsewhere on the board
ADC-3C: J7.3; also elsewhere on the board
ADC-3D: J7.4; also elsewhere on the board
ADC-4A: J10.1; also elsewhere on the board
ADC-4B: J10.2; also elsewhere on the board
ADC-4C: J10.3; also elsewhere on the board
ADC-4D: J10.4; also elsewhere on the board
CS-1: J3.5, R2.2; also elsewhere on the board
CS-2: J5.5, R18.2; also elsewhere on the board
CS-3: J8.5, R19.2; also elsewhere on the board
CS-4: J11.5, R20.2; also elsewhere on the board
Free-1: J13.5, J13.26; also elsewhere on the board
Free-2: J16.5, J16.26; also elsewhere on the board
GND: J3.3, J3.7, J5.3, J5.7, J8.3, J8.7, J11.3, J11.7, J12.2, J13.7, J13.8, J13.15, J13.16, J13.23, J13.24, J13.MP (MountPin), J16.7, J16.8, J16.15, J16.16, J16.23, J16.24, J16.MP (MountPin), J18.4; also elsewhere on the board
MISO: J3.4, J5.4, J8.4, J11.4, J13.10, J13.21, J16.10, J16.21; also elsewhere on the board
MOSI: J3.6, J5.6, J8.6, J11.6, J13.12, J13.19, J16.12, J16.19; also elsewhere on the board
NRST: J13.9, J13.22, J16.9, J16.22; also elsewhere on the board
PWM-1A: J15.1; also elsewhere on the board
PWM-1B: J15.2; also elsewhere on the board
PWM-1C: J15.3; also elsewhere on the board
PWM-1D: J15.4; also elsewhere on the board
PWM-2A: J2.1; also elsewhere on the board
PWM-2B: J2.2; also elsewhere on the board
PWM-2C: J2.3; also elsewhere on the board
PWM-2D: J2.4; also elsewhere on the board
PWM-3A: J6.1; also elsewhere on the board
PWM-3B: J6.2; also elsewhere on the board
PWM-3C: J6.3; also elsewhere on the board
PWM-3D: J6.4; also elsewhere on the board
PWM-4A: J9.1; also elsewhere on the board
PWM-4B: J9.2; also elsewhere on the board
PWM-4C: J9.3; also elsewhere on the board
PWM-4D: J9.4; also elsewhere on the board
RS485+: J12.3, J18.1; also elsewhere on the board
RS485-: J12.1, J18.3; also elsewhere on the board
SCK: J3.2, J5.2, J8.2, J11.2, J13.14, J13.17, J16.14, J16.17; also elsewhere on the board
SCL: J13.6, J13.25, J16.6, J16.25; also elsewhere on the board
SDA: J13.4, J13.27, J16.4, J16.27; also elsewhere on the board
UART0-RTS: TP20.1; also elsewhere on the board
UART0_RX: J13.13, J13.18, J16.13, J16.18, TP2.1; also elsewhere on the board
UART0_TX: J13.11, J13.20, J16.11, J16.20, TP3.1; also elsewhere on the board
VBUS: J18.2; also elsewhere on the board
VDD: J3.1, J5.1, J8.1, J11.1, J12.4, J13.1, J13.2, J13.29, J13.30, J16.1, J16.2, J16.29, J16.30, R2.1, R18.1, R19.1, R20.1; also elsewhere on the board

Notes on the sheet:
Male
Communication/Chaining/Stacking Connectors
Motor Drivers
Female
DEBUG pins
Maybe buffer the clock net and MOSI. Won't screw up edges depending offboard stuff. SN74LVC2G17
Reverse orientation top side receptacles, all pins are the same on both sides. This hub can hold two sensors
CS pullup helps during device startup and decreases randomness
Can't populate due to parts not being available from China. Will have to manually populate
All connectors need: SPI, I2C, programming, and 1 multipurpose pin. Beyond that, nothing is gaurunteed (what do the free pins do, are they different on each side, etc...)
VBUS - Hotswap controller power input. Chained together, so VDD is up top
Female. The male connector is 852-10-004-20-001101 or 852-80-004-20-001101

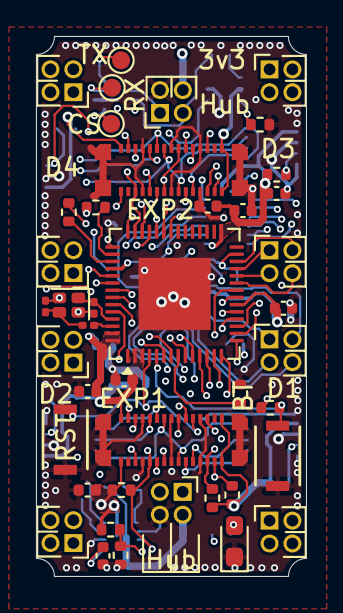
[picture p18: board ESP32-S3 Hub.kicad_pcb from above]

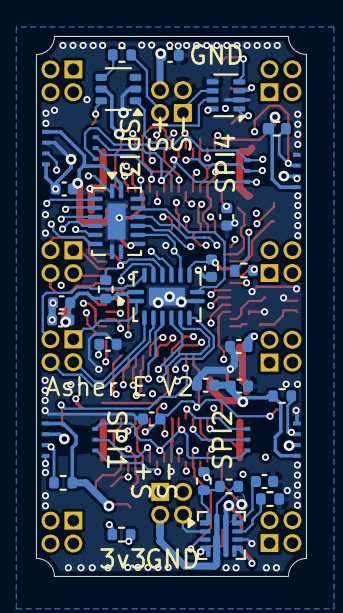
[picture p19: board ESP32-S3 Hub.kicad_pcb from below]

Board: 6 copper layers, 15.0 x 30.0 mm, 73 parts (31 on the bottom side), 74 nets.

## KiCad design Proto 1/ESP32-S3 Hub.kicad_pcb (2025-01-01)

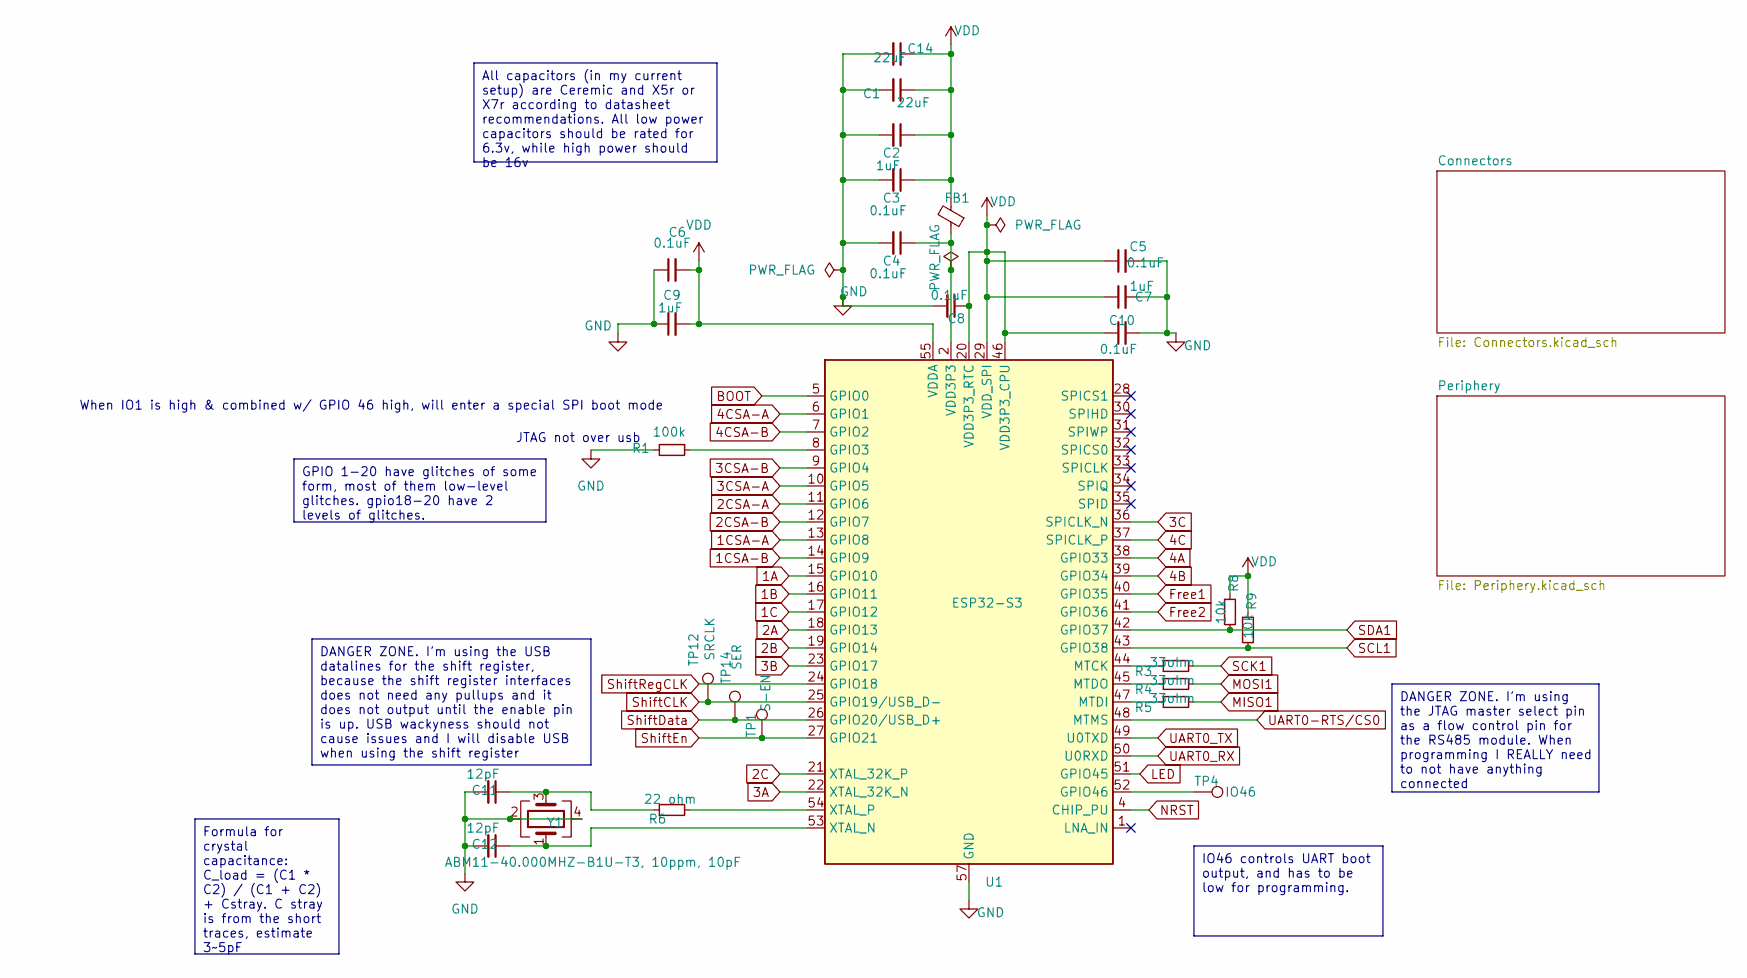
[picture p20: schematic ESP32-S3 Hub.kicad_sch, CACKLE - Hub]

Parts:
C1, C14: 22uF; C_0402_1005Metric; LCSC C415703
C2, C7, C9: 1uF; C_0402_1005Metric; LCSC C52923
C3, C4, C5, C6, C8, C10: 0.1uF; C_0402_1005Metric; LCSC C1525
C11, C12: 12pF; C_0402_1005Metric; LCSC C1547
FB1: 120ohm imp @100mhz, 1 amp; L_0402_1005Metric; LCSC C82861
R1: 100k; R_0402_1005Metric; LCSC C25741
R3, R4, R5: 33ohm; R_0402_1005Metric; LCSC C25105
R6: 22 ohm; R_0402_1005Metric; LCSC C25092
R8, R9: 10k; R_0402_1005Metric; LCSC C25744
TP1: S-EN; TestPoint_Pad_D1.0mm
TP4: IO46; TestPoint_Pad_D1.0mm
TP12: SRCLK; TestPoint_Pad_D1.0mm
TP14: SER; TestPoint_Pad_D1.0mm
U1: ESP32-S3; QFN-56-1EP_7x7mm_P0.4mm_EP4x4mm; LCSC C3013940
Y1: ABM11-40.000MHZ-B1U-T3, 10ppm, 10pF; Crystal_SMD_2016-4Pin_2.0x1.6mm; LCSC C648973

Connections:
1A: U1.15 (GPIO10); also elsewhere on the board
1B: U1.16 (GPIO11); also elsewhere on the board
1C: U1.17 (GPIO12); also elsewhere on the board
1CSA-A: U1.13 (GPIO8); also elsewhere on the board
1CSA-B: U1.14 (GPIO9); also elsewhere on the board
2A: U1.18 (GPIO13); also elsewhere on the board
2B: U1.19 (GPIO14); also elsewhere on the board
2C: U1.21 (XTAL_32K_P); also elsewhere on the board
2CSA-A: U1.11 (GPIO6); also elsewhere on the board
2CSA-B: U1.12 (GPIO7); also elsewhere on the board
3A: U1.22 (XTAL_32K_N); also elsewhere on the board
3B: U1.23 (GPIO17); also elsewhere on the board
3C: U1.36 (SPICLK_N); also elsewhere on the board
3CSA-A: U1.10 (GPIO5); also elsewhere on the board
3CSA-B: U1.9 (GPIO4); also elsewhere on the board
4A: U1.38 (GPIO33); also elsewhere on the board
4B: U1.39 (GPIO34); also elsewhere on the board
4C: U1.37 (SPICLK_P); also elsewhere on the board
4CSA-A: U1.6 (GPIO1); also elsewhere on the board
4CSA-B: U1.7 (GPIO2); also elsewhere on the board
BOOT: U1.5 (GPIO0); also elsewhere on the board
Free1: U1.40 (GPIO35); also elsewhere on the board
Free2: U1.41 (GPIO36); also elsewhere on the board
GND: C1.2, C2.2, C3.2, C4.2, C5.2, C6.1, C7.2, C8.2, C9.1, C10.2, C11.2, C12.2, C14.2, R1.2, U1.57 (GND), Y1.2, Y1.4; also elsewhere on the board
LED: U1.51 (GPIO45); also elsewhere on the board
MISO1: R5.2; also elsewhere on the board
MOSI1: R4.2; also elsewhere on the board
NRST: U1.4 (CHIP_PU); also elsewhere on the board
unnamed: C4.1, FB1.1, U1.2 (VDD3P3), U1.3 (VDD3P3)
unnamed: C11.1, R6.1, Y1.3
unnamed: R1.1, U1.8 (GPIO3)
unnamed: TP4.1, U1.52 (GPIO46)
unnamed: R3.1, U1.44 (MTCK)
unnamed: R5.1, U1.47 (MTDI)
unnamed: R4.1, U1.45 (MTDO)
unnamed: C12.1, U1.53 (XTAL_N), Y1.1
unnamed: R6.2, U1.54 (XTAL_P)
SCK1: R3.2; also elsewhere on the board
SCL1: R9.2, U1.43 (GPIO38); also elsewhere on the board
SDA1: R8.2, U1.42 (GPIO37); also elsewhere on the board
ShiftCLK: TP12.1, U1.25 (GPIO19/USB_D-); also elsewhere on the board
ShiftData: TP14.1, U1.26 (GPIO20/USB_D+); also elsewhere on the board
ShiftEn: TP1.1, U1.27 (GPIO21); also elsewhere on the board
ShiftRegCLK: U1.24 (GPIO18); also elsewhere on the board
UART0-RTS/CS0: U1.48 (MTMS); also elsewhere on the board
UART0_RX: U1.50 (U0RXD); also elsewhere on the board
UART0_TX: U1.49 (U0TXD); also elsewhere on the board
VDD: C1.1, C2.1, C3.1, C5.1, C6.2, C7.1, C8.1, C9.2, C10.1, C14.1, FB1.2, R8.1, R9.1, U1.20 (VDD3P3_RTC), U1.29 (VDD_SPI), U1.46 (VDD3P3_CPU), U1.55 (VDDA), U1.56 (VDDA); also elsewhere on the board

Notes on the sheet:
DANGER ZONE. I'm using the JTAG master select pin as a flow control pin for the RS485 module. When programming I REALLY need to not have anything connected
DANGER ZONE. I'm using the USB datalines for the shift register, because the shift register interfaces does not need any pullups and it does not output until the enable pin is up. USB wackyness should not cause issues and I will disable USB when using the shift register
All capacitors (in my current setup) are Ceremic and X5r or X7r according to datasheet recommendations. All low power capacitors should be rated for 6.3v, while high power should be 16v
IO46 controls UART boot output, and has to be low for programming.
GPIO 1-20 have glitches of some form, most of them low-level glitches. gpio18-20 have 2 levels of glitches.
Formula for crystal capacitance: C_load = (C1 * C2) / (C1 + C2) + Cstray. C stray is from the short traces, estimate 3~5pF
JTAG not over usb
When IO1 is high & combined w/ GPIO 46 high, will enter a special SPI boot mode

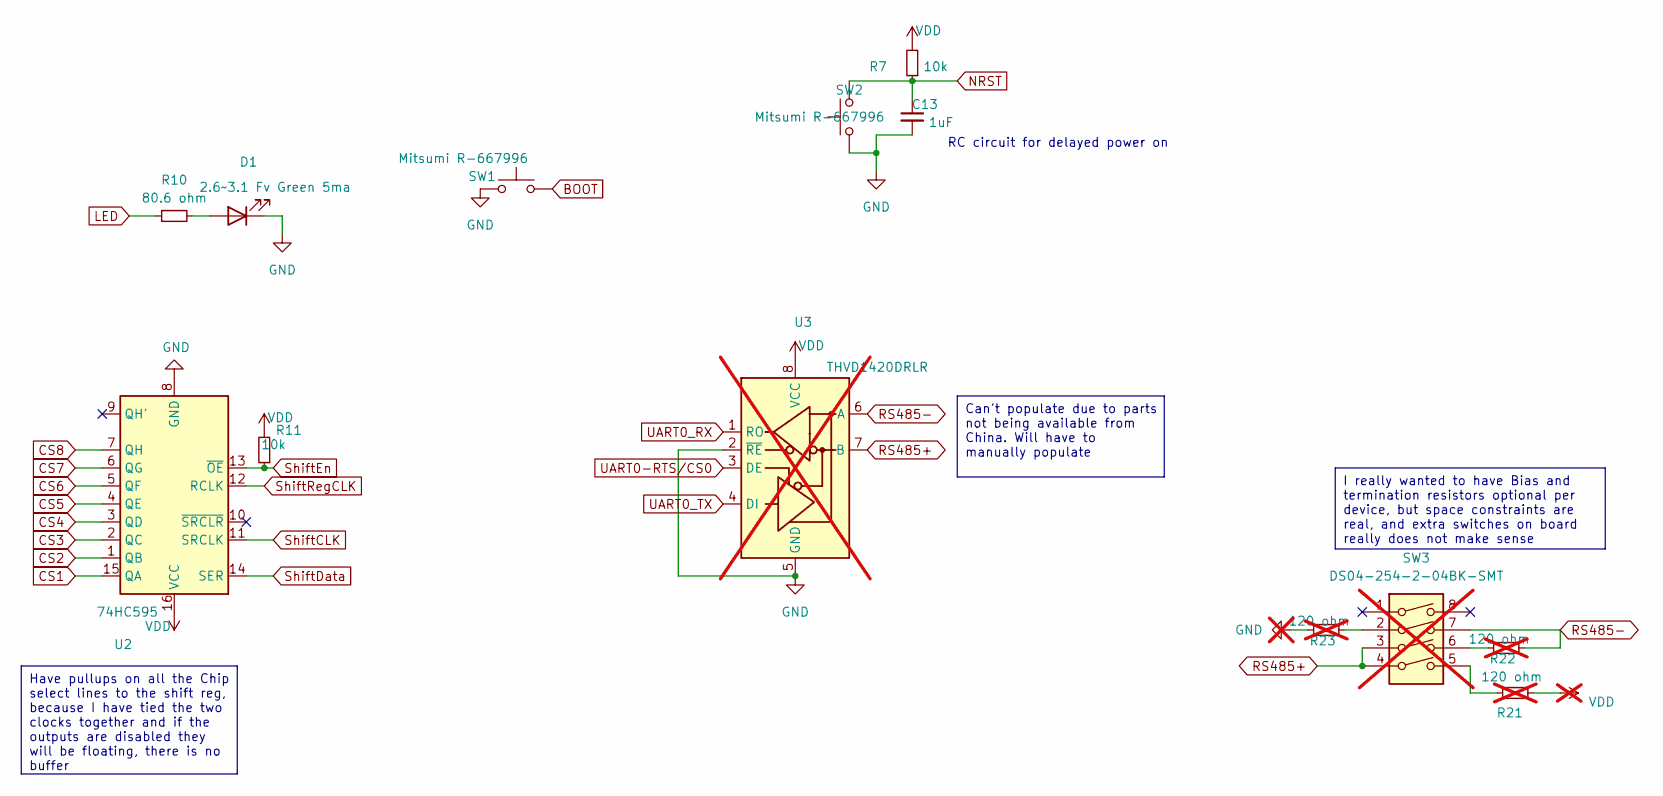
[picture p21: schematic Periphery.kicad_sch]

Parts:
C13: 1uF; C_0402_1005Metric; LCSC C52923
D1: 2.6~3.1 Fv Green 5ma; LED_0603_1608Metric_Pad1.05x0.95mm_HandSolder; LCSC C3028858
R7, R11: 10k; R_0402_1005Metric; LCSC C25744
R10: 80.6 ohm; R_0402_1005Metric; LCSC C185392
R21, R22, R23: 120 ohm; R_0402_1005Metric; not fitted
SW1, SW2: Mitsumi R-667996; R-667995_MIT; LCSC C4365007
SW3: DS04-254-2-04BK-SMT; SW_DIP_SPSTx04_Slide_Omron_A6S-410x_W8.9mm_P2.54mm; not fitted
U2: 74HC595; DHVQFN-16-1EP_2.5x3.5mm_P0.5mm_EP1x2mm; LCSC C730243
U3: THVD1420DRLR; SOT-583-8; not fitted

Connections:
BOOT: SW1.2; also elsewhere on the board
CS1: U2.15 (QA); also elsewhere on the board
CS2: U2.1 (QB); also elsewhere on the board
CS3: U2.2 (QC); also elsewhere on the board
CS4: U2.3 (QD); also elsewhere on the board
CS5: U2.4 (QE); also elsewhere on the board
CS6: U2.5 (QF); also elsewhere on the board
CS7: U2.6 (QG); also elsewhere on the board
CS8: U2.7 (QH); also elsewhere on the board
GND: C13.2, D1.1 (K), R23.2, SW1.1, SW2.1, U2.8 (GND), U2.17 (GND), U3.2 (~RE), U3.5 (GND); also elsewhere on the board
LED: R10.1; also elsewhere on the board
NRST: C13.1, R7.1, SW2.2; also elsewhere on the board
unnamed: D1.2 (A), R10.2
unnamed: R21.2, SW3.5
unnamed: R22.2, SW3.6
unnamed: R23.1, SW3.2
RS485+: SW3.3, SW3.4, U3.7 (B); also elsewhere on the board
RS485-: R22.1, SW3.7, U3.6 (A); also elsewhere on the board
ShiftCLK: U2.11 (SRCLK); also elsewhere on the board
ShiftData: U2.14 (SER); also elsewhere on the board
ShiftEn: R11.1, U2.13 (~OE); also elsewhere on the board
ShiftRegCLK: U2.12 (RCLK); also elsewhere on the board
UART0-RTS/CS0: U3.3 (DE); also elsewhere on the board
UART0_RX: U3.1 (RO); also elsewhere on the board
UART0_TX: U3.4 (DI); also elsewhere on the board
VDD: R7.2, R11.2, R21.1, U2.16 (VCC), U3.8 (VCC); also elsewhere on the board

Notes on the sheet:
Can't populate due to parts not being available from China. Will have to manually populate
Have pullups on all the Chip select lines to the shift reg, because I have tied the two clocks together and if the outputs are disabled they will be floating, there is no buffer
I really wanted to have Bias and termination resistors optional per device, but space constraints are real, and extra switches on board really does not make sense
RC circuit for delayed power on

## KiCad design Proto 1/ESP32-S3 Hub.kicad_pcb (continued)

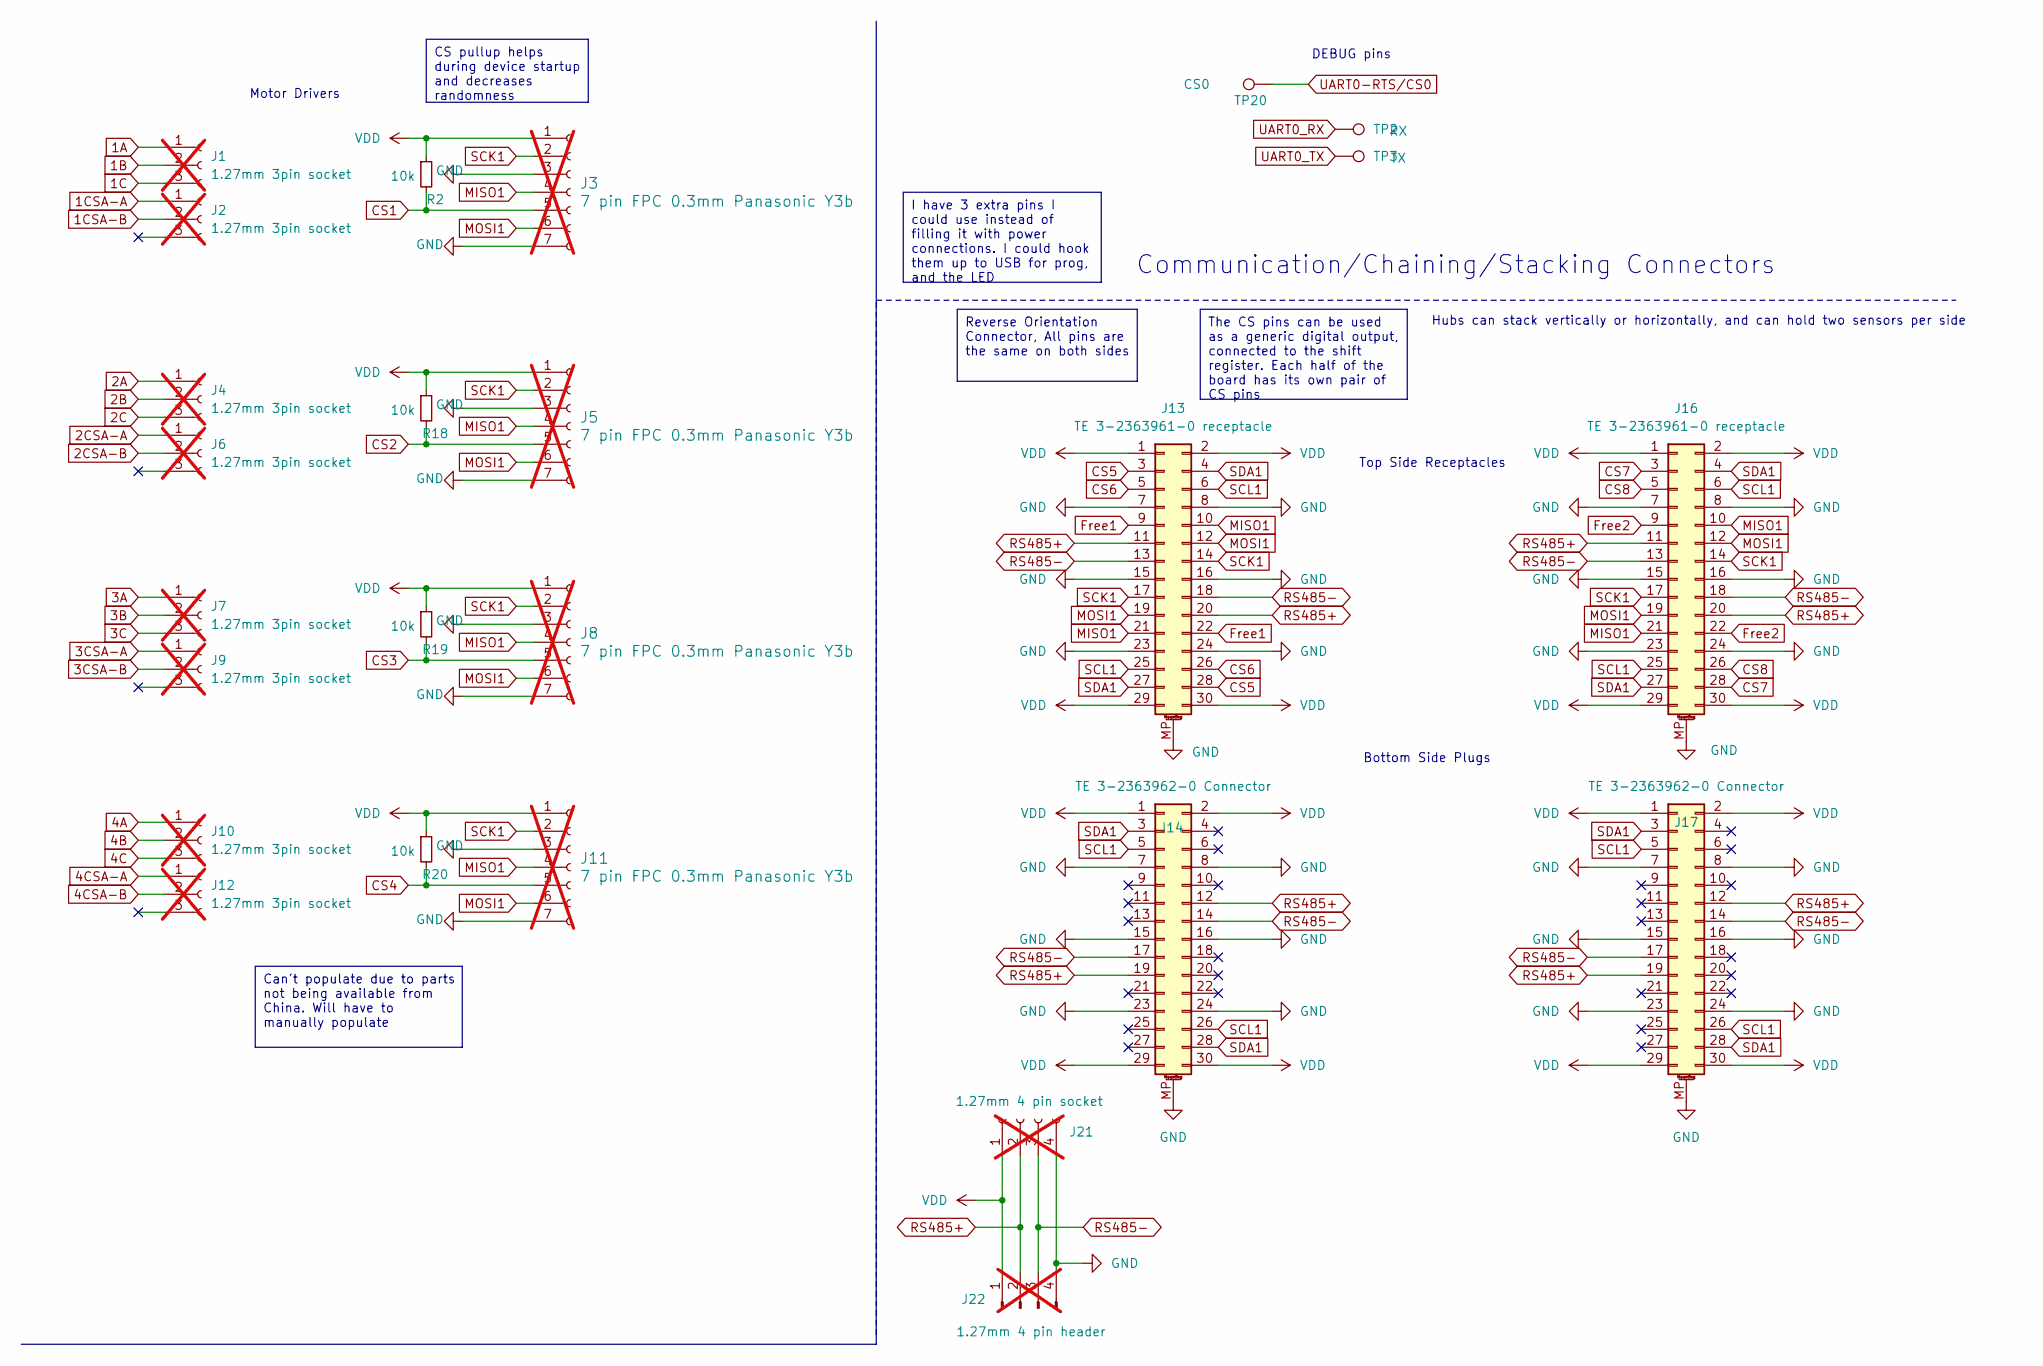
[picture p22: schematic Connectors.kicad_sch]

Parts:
J1, J2, J4, J6, J7, J9, J10, J12: 1.27mm 3pin socket; PinHeader_1x03_P1.27mm_Vertical; not fitted
J3, J5, J8, J11: 7 pin FPC 0.3mm Panasonic Y3b; fpc_7pin_0.3mm_connector Panasonic; not fitted
J13, J16: TE 3-2363961-0 receptacle; TE_mezzanine_rec_3-2363961-0; LCSC C425103
J14, J17: TE 3-2363962-0 Connector; TE_mezzanine_conn_3-2363962-0; LCSC C425104
J21: 1.27mm 4 pin socket; PinSocket_1x04_P1.27mm_Vertical; not fitted
J22: 1.27mm 4 pin header; PinHeader_1x04_P1.27mm_Horizontal; not fitted
R2, R18, R19, R20: 10k; R_0402_1005Metric; LCSC C25744
TP2: RX; TestPoint_Pad_D1.0mm
TP3: TX; TestPoint_Pad_D1.0mm
TP20: CS0; TestPoint_Pad_D1.0mm

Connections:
1A: J1.1; also elsewhere on the board
1B: J1.2; also elsewhere on the board
1C: J1.3; also elsewhere on the board
1CSA-A: J2.1; also elsewhere on the board
1CSA-B: J2.2; also elsewhere on the board
2A: J4.1; also elsewhere on the board
2B: J4.2; also elsewhere on the board
2C: J4.3; also elsewhere on the board
2CSA-A: J6.1; also elsewhere on the board
2CSA-B: J6.2; also elsewhere on the board
3A: J7.1; also elsewhere on the board
3B: J7.2; also elsewhere on the board
3C: J7.3; also elsewhere on the board
3CSA-A: J9.1; also elsewhere on the board
3CSA-B: J9.2; also elsewhere on the board
4A: J10.1; also elsewhere on the board
4B: J10.2; also elsewhere on the board
4C: J10.3; also elsewhere on the board
4CSA-A: J12.1; also elsewhere on the board
4CSA-B: J12.2; also elsewhere on the board
CS1: J3.5, R2.2; also elsewhere on the board
CS2: J5.5, R18.2; also elsewhere on the board
CS3: J8.5, R19.2; also elsewhere on the board
CS4: J11.5, R20.2; also elsewhere on the board
CS5: J13.3, J13.28; also elsewhere on the board
CS6: J13.5, J13.26; also elsewhere on the board
CS7: J16.3, J16.28; also elsewhere on the board
CS8: J16.5, J16.26; also elsewhere on the board
Free1: J13.9, J13.22; also elsewhere on the board
Free2: J16.9, J16.22; also elsewhere on the board
GND: J3.3, J3.7, J5.3, J5.7, J8.3, J8.7, J11.3, J11.7, J13.7, J13.8, J13.15, J13.16, J13.23, J13.24, J13.MP (MountPin), J14.7, J14.8, J14.15, J14.16, J14.23, J14.24, J14.MP (MountPin), J16.7, J16.8, J16.15, J16.16, J16.23, J16.24, J16.MP (MountPin), J17.7, J17.8, J17.15, J17.16, J17.23, J17.24, J17.MP (MountPin), J21.4, J22.4; also elsewhere on the board
MISO1: J3.4, J5.4, J8.4, J11.4, J13.10, J13.21, J16.10, J16.21; also elsewhere on the board
MOSI1: J3.6, J5.6, J8.6, J11.6, J13.12, J13.19, J16.12, J16.19; also elsewhere on the board
RS485+: J13.11, J13.20, J14.12, J14.19, J16.11, J16.20, J17.12, J17.19, J21.2, J22.2; also elsewhere on the board
RS485-: J13.13, J13.18, J14.14, J14.17, J16.13, J16.18, J17.14, J17.17, J21.3, J22.3; also elsewhere on the board
SCK1: J3.2, J5.2, J8.2, J11.2, J13.14, J13.17, J16.14, J16.17; also elsewhere on the board
SCL1: J13.6, J13.25, J14.5, J14.26, J16.6, J16.25, J17.5, J17.26; also elsewhere on the board
SDA1: J13.4, J13.27, J14.3, J14.28, J16.4, J16.27, J17.3, J17.28; also elsewhere on the board
UART0-RTS/CS0: TP20.1; also elsewhere on the board
UART0_RX: TP2.1; also elsewhere on the board
UART0_TX: TP3.1; also elsewhere on the board
VDD: J3.1, J5.1, J8.1, J11.1, J13.1, J13.2, J13.29, J13.30, J14.1, J14.2, J14.29, J14.30, J16.1, J16.2, J16.29, J16.30, J17.1, J17.2, J17.29, J17.30, J21.1, J22.1, R2.1, R18.1, R19.1, R20.1; also elsewhere on the board

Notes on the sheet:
Reverse Orientation Connector, All pins are the same on both sides
CS pullup helps during device startup and decreases randomness
Can't populate due to parts not being available from China. Will have to manually populate
The CS pins can be used as a generic digital output, connected to the shift register. Each half of the board has its own pair of CS pins
I have 3 extra pins I could use instead of filling it with power connections. I could hook them up to USB for prog, and the LED
Communication/Chaining/Stacking Connectors
Top Side Receptacles
Motor Drivers
Hubs can stack vertically or horizontally, and can hold two sensors per side
DEBUG pins
Bottom Side Plugs

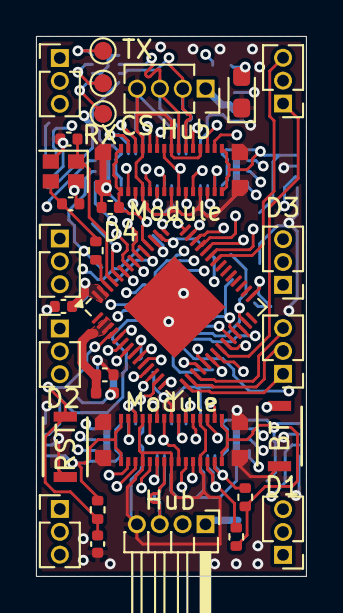
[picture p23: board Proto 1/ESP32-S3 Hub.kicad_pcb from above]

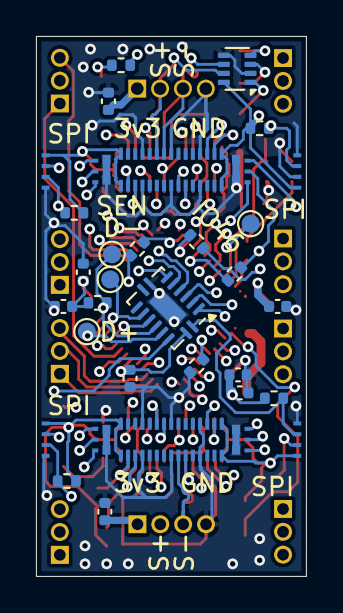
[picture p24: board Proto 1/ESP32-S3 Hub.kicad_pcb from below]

Board: 6 copper layers, 15.0 x 30.0 mm, 61 parts (30 on the bottom side), 59 nets.

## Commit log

2024-12-31 Rearranged design files
    Instead of "Kicad" the main design folder is now named "Hardware" since I have gerbers and notes besides the kicad files. I have also put my designs in their proper categories.
    [Connectors.kicad_sch, ESP32-S3 Hub Main BOM.csv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]
2025-01-01 Updated files for JLC DFM checks
    [ESP32-S3 Hub.kicad_pcb, positions.csv]
2025-01-02 Added schematic PDFs for all boards
2025-01-04 Added gerber zip files
2025-01-13 Changed link names for schematic embeds not displayin
    In Obsidian I can see the pdf embeds perfectly fine, but Github doesn't want to show embedded PDFs. I changed the link alias to "Schematic PDF" so people know what the link is when it doesn't display
2025-02-02 Hardware Revision folder restructuring
    [Connectors.kicad_sch, ESP32-S3 Hub Main BOM.csv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]
2025-10-10 Revert Separation of hardare versions
    This folder versioning will be limited to production files only now
    [Connectors.kicad_sch, ESP32-S3 Hub Main BOM.csv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]
2025-10-10 Started Proto 2 again
    [Connectors.kicad_sch, ESP32-S3 Hub Main BOM.csv, ESP32-S3 Hub.kicad_pcb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]
2025-10-12 Updated connectors in schem and pcb
    [Connectors.kicad_sch, ESP32-S3 Hub.kicad_pcb, ESP32-S3 Hub.kicad_sch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]
2025-10-12 Updated component arrangements and fixed pinout on upstream port
    [Connectors.kicad_sch, ESP32-S3 Hub.kicad_pcb]
2025-10-17 Removed bottom side connectors due to infeasability for expansion
    Only 4 port mcu hubs could have the double sided expansion unless the MCU was a BGA stuffed away in a corner, so it wouldn't be a common feature. Also it adds a ton of complexity for the RS r485 line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
    [Connectors.kicad_sch]
2025-10-17 Add 5mil traces & 0.4mm vias, started via placement
    I am decreasing the size further to speed up routing and avoid pain. The cost will be higher, but not that much higher from 0.3mm to 0.2mm and 0.6mm to 0.4mm vias. I can route more items.
    [ESP32-S3 Hub.kicad_pcb]
2025-10-17 Fix some track sizes and clearance issues
    [ESP32-S3 Hub.kicad_pcb]
2025-10-26 Changed peripheral, tied PWM to shift reg, program pins
    [Connectors.kicad_sch, ESP32-S3 Hub.kicad_sch, Periphery.kicad_sch]
2025-10-26 Swapped out footprints on pcb, started routing
    [ESP32-S3 Hub.kicad_pcb]
2025-10-31 Added future design expansion comments, re arrange components to fit better
    [Connectors.kicad_sch, ESP32-S3 Hub.kicad_pcb, ESP32-S3 Hub.kicad_sch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]
2025-10-31 Finish connector schematic
    [Connectors.kicad_sch]
2025-11-01 Swapped around pins and routed main driver outputs
    [ESP32-S3 Hub.kicad_pcb, ESP32-S3 Hub.kicad_sch, Periphery.kicad_sch]
2025-11-01 Finished routing with current components
    I may add some protection and isolation stuff
    [ESP32-S3 Hub.kicad_pcb, ESP32-S3 Hub.kicad_sch]
2025-11-02 Started power protection hotswap circuit
    [Connectors.kicad_sch, Periphery.kicad_sch]
2025-11-03 Replaced LED driver with 2 shift registers
    My initial approach from the first version was better design, I need 80+ mhz to get adequate PWM signals.
    [ESP32-S3 Hub.kicad_sch, Periphery.kicad_sch]
2025-11-04 Added configurable termination with analog switch
    [Periphery.kicad_sch]
2025-11-04 Added shift reg footprints
    [Periphery.kicad_sch]
2025-11-04 Got proper values and replacement eFuse
    [Connectors.kicad_sch, ESP32-S3 Hub.kicad_sch, Periphery.kicad_sch]
2025-11-05 Reorganized and made schematic clearer
    [Connectors.kicad_sch, Periphery.kicad_sch]
2025-11-05 Corrected footprint, started reconnect nets PCB
    [ESP32-S3 Hub.kicad_pcb, ESP32-S3 Hub.kicad_sch, Periphery.kicad_sch]
2025-11-06 Finished Reroute of ESP32-s3 hub
    [ESP32-S3 Hub.kicad_pcb, ESP32-S3 Hub.kicad_sch, Periphery.kicad_sch]
2025-11-08 Moved stencil jig from monorepo to here
    [ESP32-S3 2nd side Stencil Jig.step]
2025-11-08 Improve schematic consistency
    [Connectors.kicad_sch, ESP32-S3 Hub.kicad_sch, Periphery.kicad_sch]
2025-11-08 Removed unnecessary ferrite bead
    There is no radio on this design to worry about power coupling
    [ESP32-S3 Hub.kicad_sch]
2025-11-08 Clarified capacitors for main chip
    [ESP32-S3 Hub.kicad_sch]
2025-11-08 Fixed ERC power flag issues
    [ESP32-S3 Hub.kicad_sch, Periphery.kicad_sch]
2025-11-08 Updated schematic symbols
    [Connectors.kicad_sch, ESP32-S3 Hub.kicad_sch, Periphery.kicad_sch]
2025-11-08 Fixed typos with ADC-4 pins, split a few circuits
    [Connectors.kicad_sch, ESP32-S3 Hub.kicad_sch, Periphery.kicad_sch]
2025-11-08 Changed LED resistor value to be more standard, reduce brightness
    [Periphery.kicad_sch]
2025-11-10 Fixed symbol issue with shift register
    [Periphery.kicad_sch]
2025-11-10 Changed clock schematic layout
    [ESP32-S3 Hub.kicad_sch]
2025-11-10 Changed configurable resistor pin in schematic
    [ESP32-S3 Hub.kicad_sch, Periphery.kicad_sch]
2025-11-10 Revised routing according to new labels and components
    [ESP32-S3 Hub.kicad_pcb]
2025-11-10 Added 1 more bulk decop capacitor
    [ESP32-S3 Hub.kicad_sch]
2025-11-11 Updated potential spec for buffer
    [Connectors.kicad_sch]
2025-11-11 Decreased number of wires on power plane for more continuous signal
    [ESP32-S3 Hub.kicad_pcb]
2025-11-11 Exported Schematic pdf
2025-11-11 Added shielding vias all around edge
    [ESP32-S3 Hub.kicad_pcb]
2025-11-11 Fixed silkscreen and traces according to DRC
    [ESP32-S3 Hub.kicad_pcb]
2025-11-14 Fixed BOM LCSC part numbers mostly
    [Connectors.kicad_sch, ESP32-S3 Hub.kicad_pcb, ESP32-S3 Hub.kicad_sch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]
2025-11-14 Updated 3D models
    [Connectors.kicad_sch, ESP32-S3 Hub.kicad_pcb]
2025-11-14 Updated Schematic PDF
2025-11-14 Updated Silkscreen, version info
    [ESP32-S3 Hub.kicad_pcb]
2025-11-14 Aggressive reroute 1 for proper connection
    [ESP32-S3 Hub.kicad_pcb]
2025-11-14 Added production files and logo to pcb
    [ESP32-S3 Hub.kicad_pcb, ESP32-S3 Hub.kicad_pcb_bom.csv, ESP32-S3 Hub.kicad_pcb_positions.csv]
2025-11-21 Fixed clock to be on top only, moved to 0201, separate clock signals
    [ESP32-S3 Hub.kicad_pcb, ESP32-S3 Hub.kicad_sch]
2025-11-21 Removed logo
    [ESP32-S3 Hub.kicad_pcb]
2025-11-21 Changed i2c resistors to be stronger
    The distance is really short and I was only ever planning on having a few devices per hub, so strength is increased.
    [ESP32-S3 Hub.kicad_pcb, ESP32-S3 Hub.kicad_sch]
2025-11-21 Fixed RS485 skew
    [ESP32-S3 Hub.kicad_pcb]
2025-11-21 Updated Gerbers
    [ESP32-S3 Hub.kicad_pcb, ESP32-S3 Hub.kicad_pcb_bom.csv, ESP32-S3 Hub.kicad_pcb_positions.csv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]
2025-11-21 Added corner 1mm cutouts
    Also excluded some DRC errors and updated 1 footprint
    [ESP32-S3 Hub.kicad_pcb]
2025-11-21 Found substitute part
    [Periphery.kicad_sch]
2025-11-21 Fixed missing sub part field in pcb file
    [ESP32-S3 Hub.kicad_pcb, bom.csv]

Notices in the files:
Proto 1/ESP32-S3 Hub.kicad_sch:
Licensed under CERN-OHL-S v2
